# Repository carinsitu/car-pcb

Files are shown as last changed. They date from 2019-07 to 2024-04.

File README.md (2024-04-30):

# CarInSitu PCB for RC car

This repository contains _KiCAD_ files related to RC car's PCB.

Its licensed under _GPLv3_.

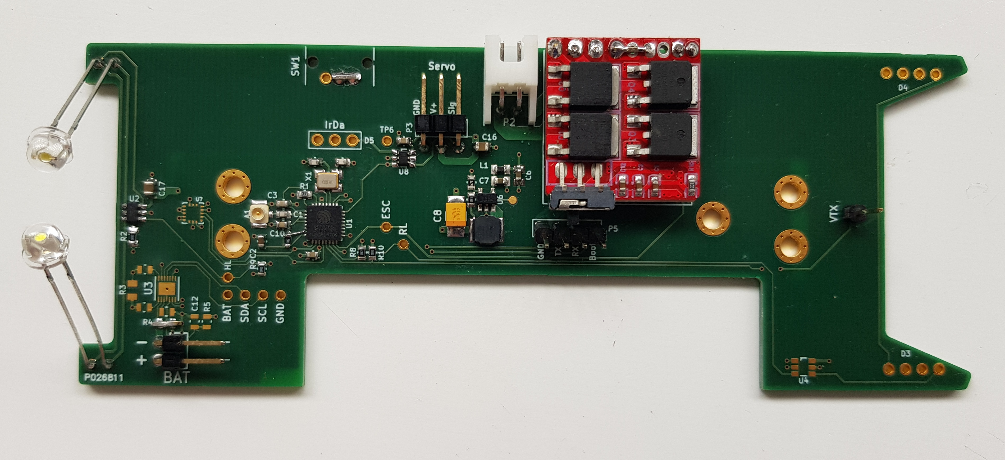
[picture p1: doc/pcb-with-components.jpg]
First Prototype


↑ The above photo is of proto 1

## Features

 - ESP82xx MCU
 - External antenna through UFL connector (using Lolin D1 mini pro)
 - Front head light (High-efficiency LEDs)
 - RBG LED port (APA106/WS2812)
 - PPM-driven ESC for brushed motor (external module based)
 - PPM-driven steering
 - IR receiver
 - VTX port (UART)
 - IMU
 - Battery gauge

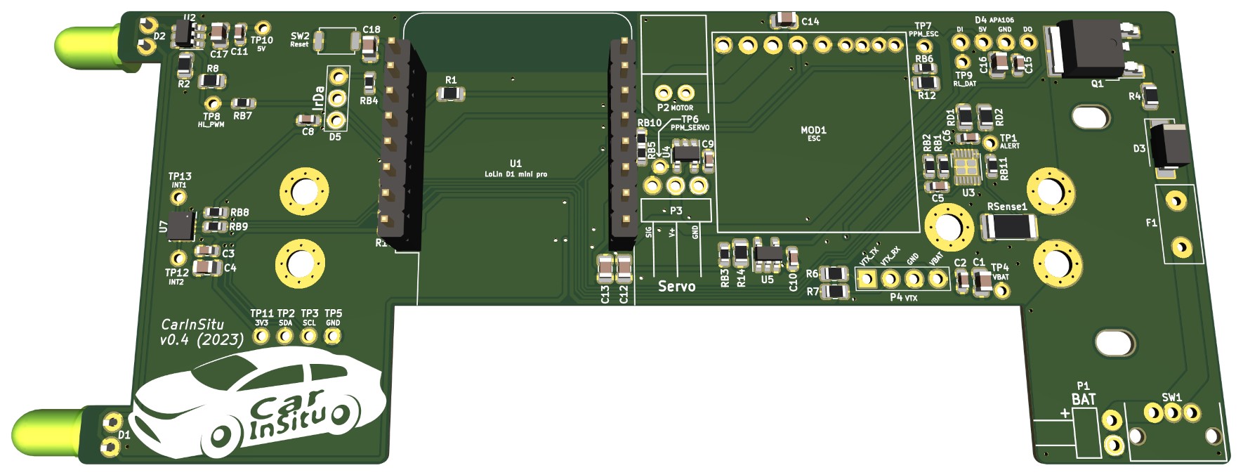
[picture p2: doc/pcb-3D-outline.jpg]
Preview of v0.4


↑ The above screenshot is a 3D preview of v0.4

## Manufacturing note

The PCB is designed with "standard" isolation (≥ 6 mil) for the most part, except in the area of the IMU (U7) whose package is just under 6 mil.

There are overlapping components:
- R1, C12, C13 with U1: U1 is high enough for this to work
- RB5 with RB10: one pad is common so that they are not on board together

## Misc

Note: Feel free to contact [neomilium](https://github.com/neomilium) if you want to turn this into commercial product.

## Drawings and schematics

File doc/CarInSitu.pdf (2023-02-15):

# SWITCH_SLIDE PWR_FLAG

LOLIN_RX_SWAP | Motor Control (ESC)

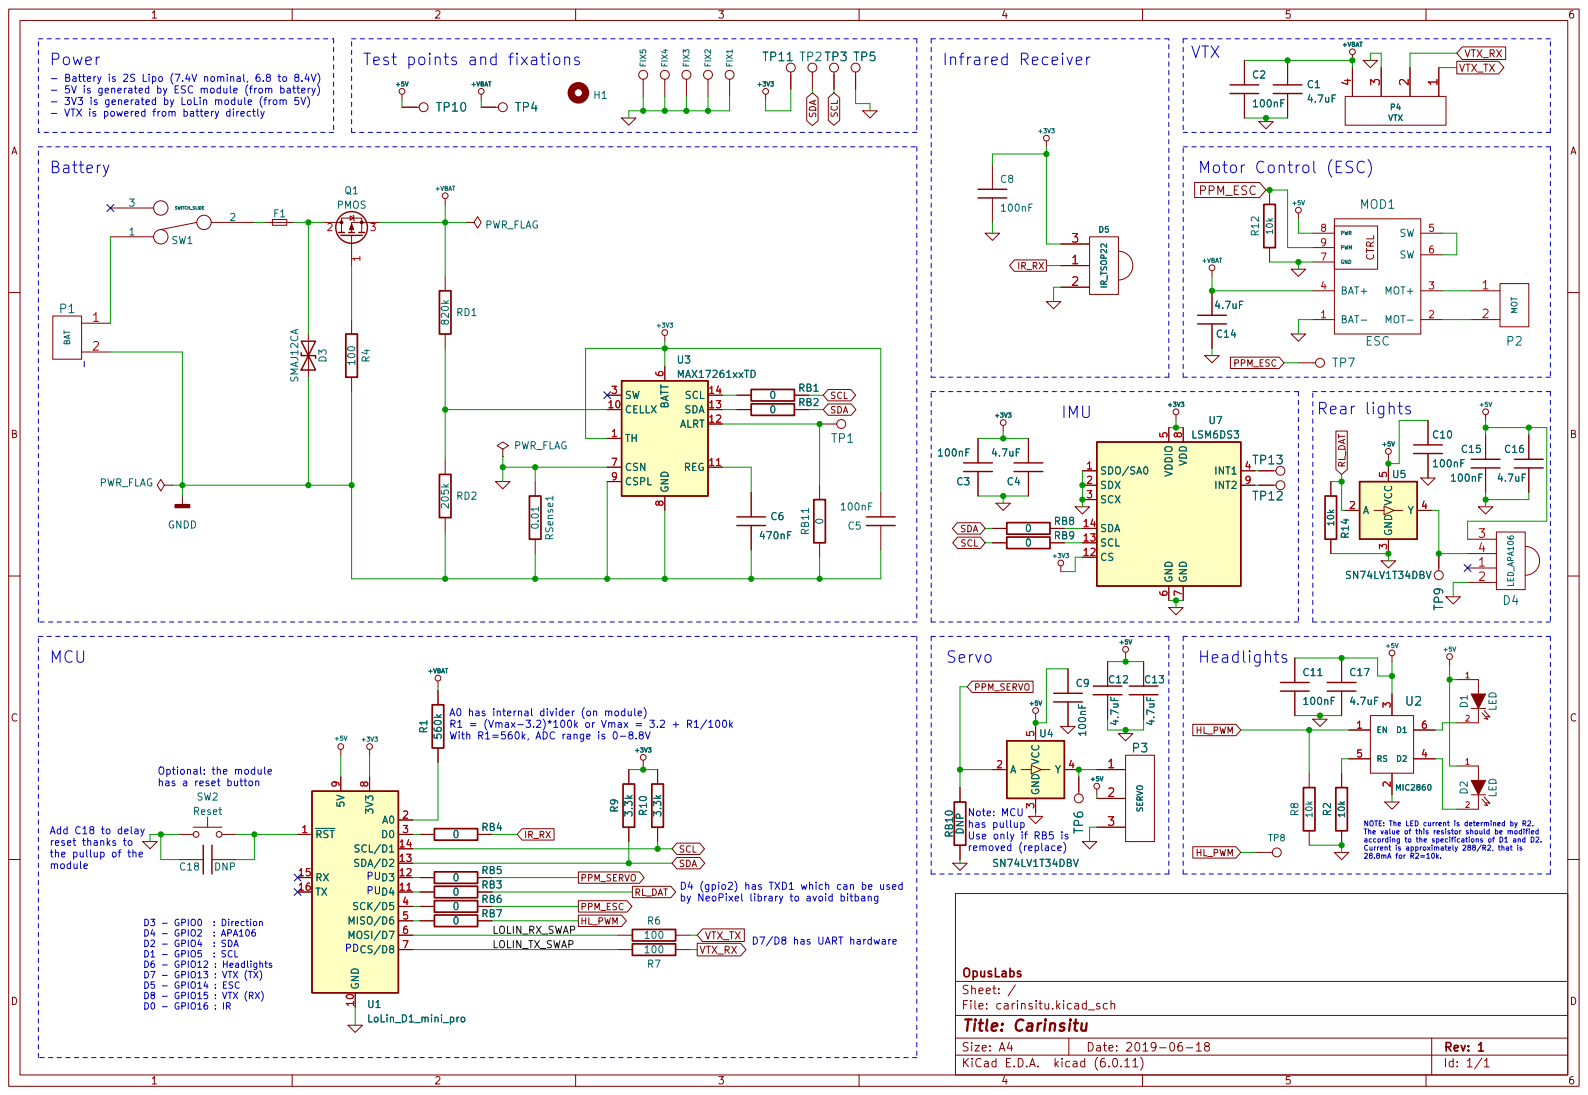
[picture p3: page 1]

Power
- VTX is powered from battery directly
the pullup of the module Battery

LSM6DS3 SDO/SA0 1 CS 12 SCL 13 SDA 14 SDX 2 SCX 3

3 SCK/D5 4 MISO/D6 5 MOSI/D7 6 CS/D8 7 ³V³

3 RB¹⁰ DNP
has pullup Use only if RB5 is

File: carinsitu.kicad_sch Sheet: / OpusLabs

References | Value | Distrib Ref Distributor | Manuf Ref | Manufacturer | Quantity
C2, C3, C5, C8, C9, C10, C11, C15 | 100nF | 2581045 | Farnell | C0603C104M4RACTU | Kemet | 8
C1, C4, C12, C13, C14, C16, C17 | 4.7uF | 2533952 | Farnell | 885012107013 | Würth elektronik | 7
C6 | 470nF | 2812270 | Farnell | 885012106015 | Würth elektronik | 1
C18 | DNP | - | - | - | - | 1
R2, R8, R12, R14 | 10k | 2073612 | Farnell | MCMR08X103JTL | Multicomp pro | 4
R4, R6, R7 | 100 | 2447552 | Farnell | MCWR08X1000FTL | Multicomp pro | 3
R9, R10 | 3.3k | 2073746 | Farnell | MCMR08X332JTL | Multicomp pro | 2
R1 | 560k | 2447685 | Farnell | MCWR08X5603FTL | Multicomp pro | 1
RD1 | 820k | 2447725 | Farnell | MCWR08X8203FTL | Multicomp pro | 1
RD2 | 205k | 2074399 | Farnell | MCSR08X2053FTL | Multicomp pro | 1
RSense1 | 0.01 | 2695180 | Farnell | MCWW20W0R01FTL | Multicomp pro | 1
RB10 | DNP | - | - | - | - | 1
D1, D2 | LED | 1716702 | Farnell | OVL-5521 | Multicomp pro | 2
D3 | SMAJ12CA | 2675283 | Farnell | SMAJ12CA+ | Multicomp pro | 1
D4 | LED_APA106 | | | | | 1
D5 | IR_TSOP22 | 4913073 | Farnell | TSOP2238 | Vishay | 1
U4, U5 | SN74LV1T34DBV | 218-4596 | RS | SN74LV1T34DBVR | Texas instruments | 2
U1 | LoLin_D1_mini_pro | | | Lolin D1 mini pro | Lolin | 1
U2 | MIC2860 | 2509995 | Farnell | MIC2860-2PYD6 | Microchip | 1
U3 | MAX17261xxTD | 2899544 | Farnell | MAX17261METD+ | Analog devices | 1
U7 | LSM6DS3 | 2664522 | Farnell | LSM6DSMTR | ST | 1
F1 | Fuse | 1345950 | Farnell | RGEF600 | LittelFuse | 1
SW1 | SWITCH_SLIDE | 2931770 | Farnell | L102011ML04Q | C&K Components | 1
SW2 | Reset | 3261823 | Farnell | SKRKAHE020 | Alps Alpine | 1
RB1, RB2, RB3, RB4, RB5, RB6, RB7, RB8, RB9, RB11 | 0 | 2447743 | Farnell | MCWR06X000PTL | Multicomp pro | 10
MOD1 | ESC | | | | | 1
Q1 | PMOS | 3518391 | Farnell | DMPH6050SK3-13 | Diodes inc. | 1
P1 | BAT | 2356176 | Farnell | 61300211021 | Würth elektronik | 1
P2 | MOT | 1516289 | Farnell | S2B-XH-A | JST | 1
P3 | SERVO | 3049557 | Farnell | 22-28-8030 | Molex | 1
P4 | VTX | - | - | - | - | 1

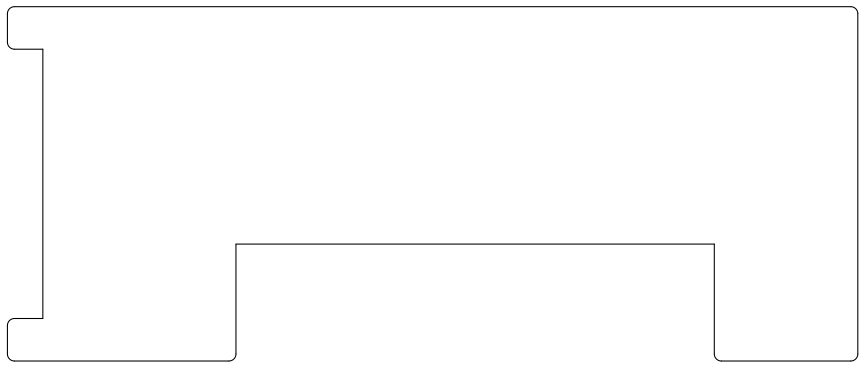
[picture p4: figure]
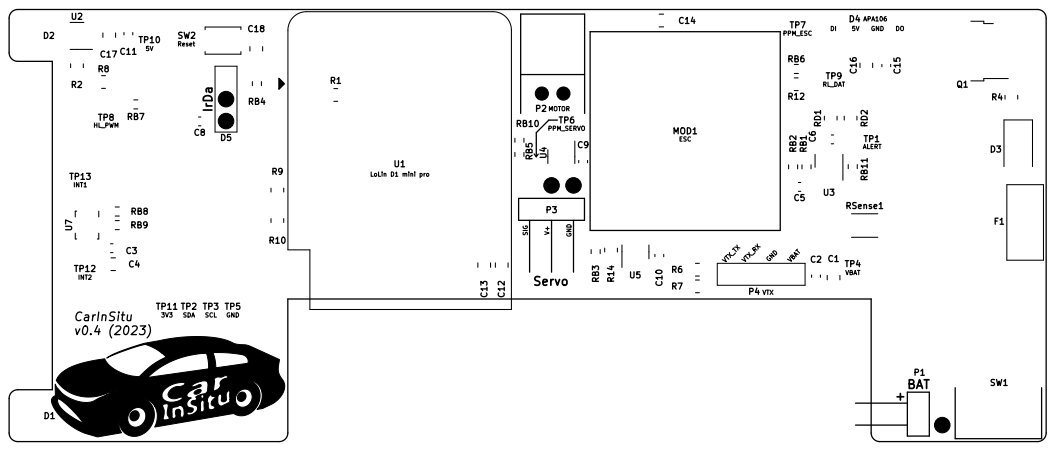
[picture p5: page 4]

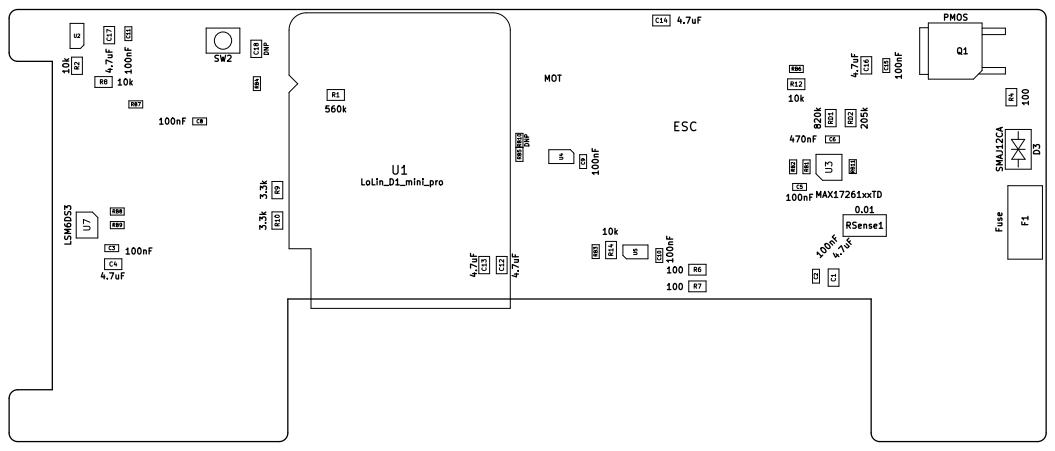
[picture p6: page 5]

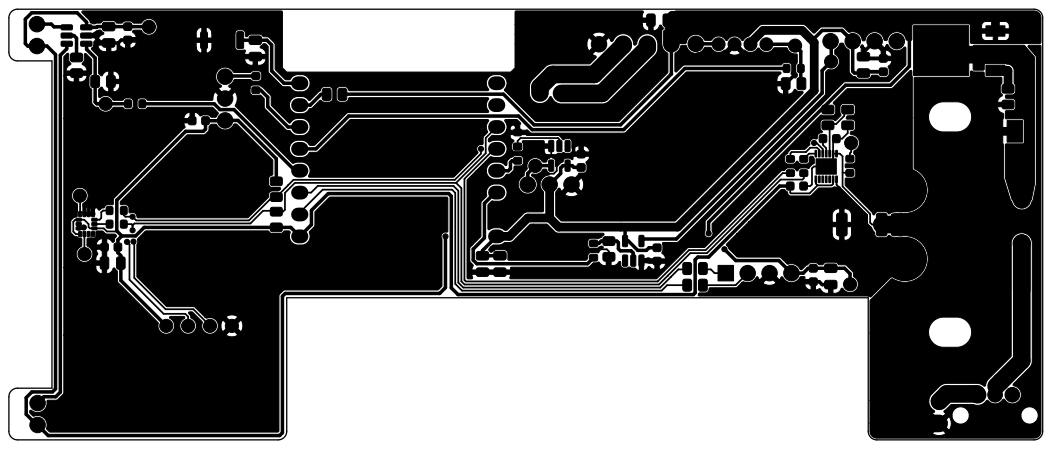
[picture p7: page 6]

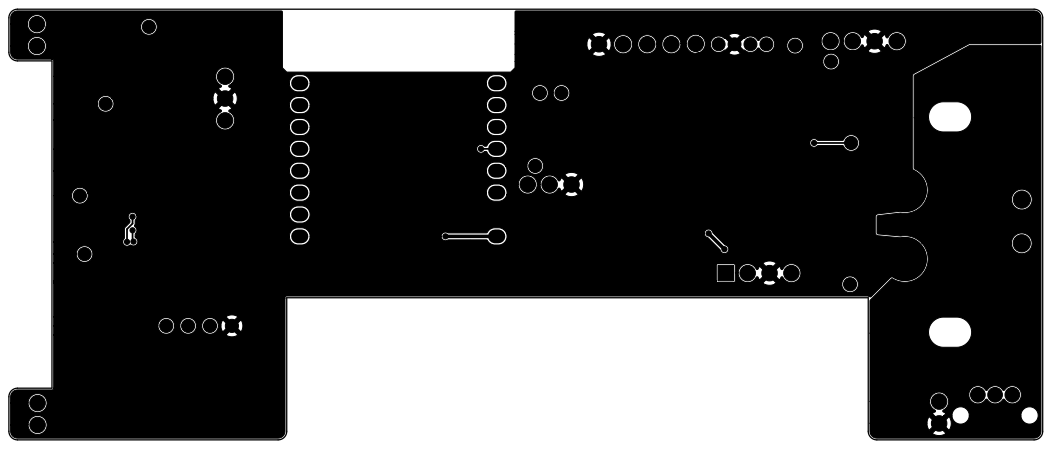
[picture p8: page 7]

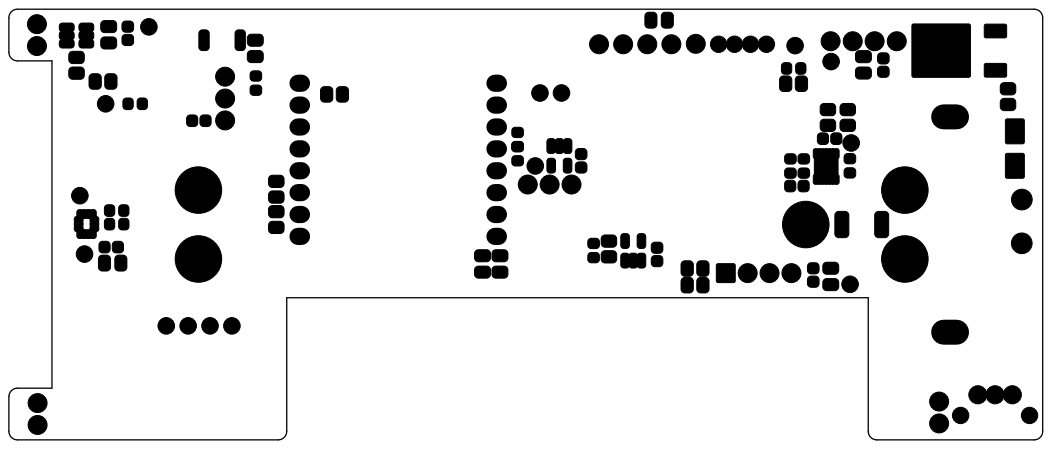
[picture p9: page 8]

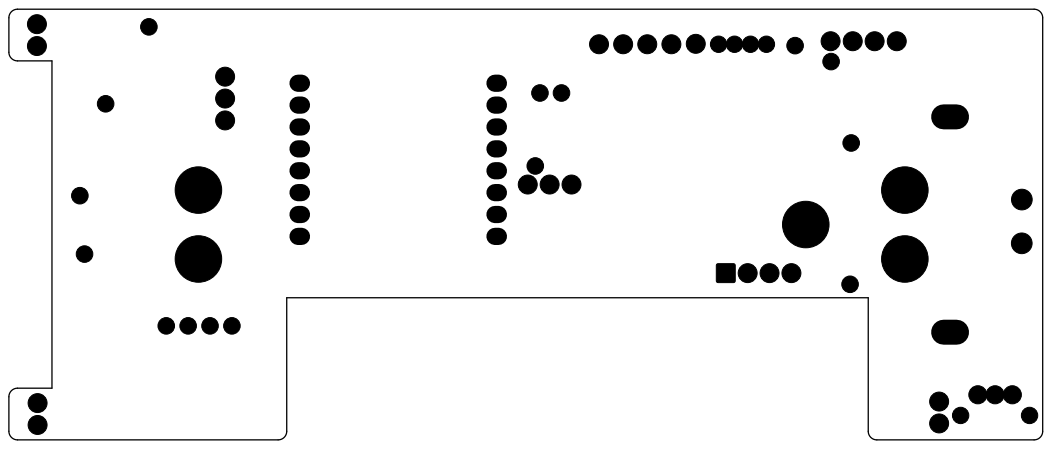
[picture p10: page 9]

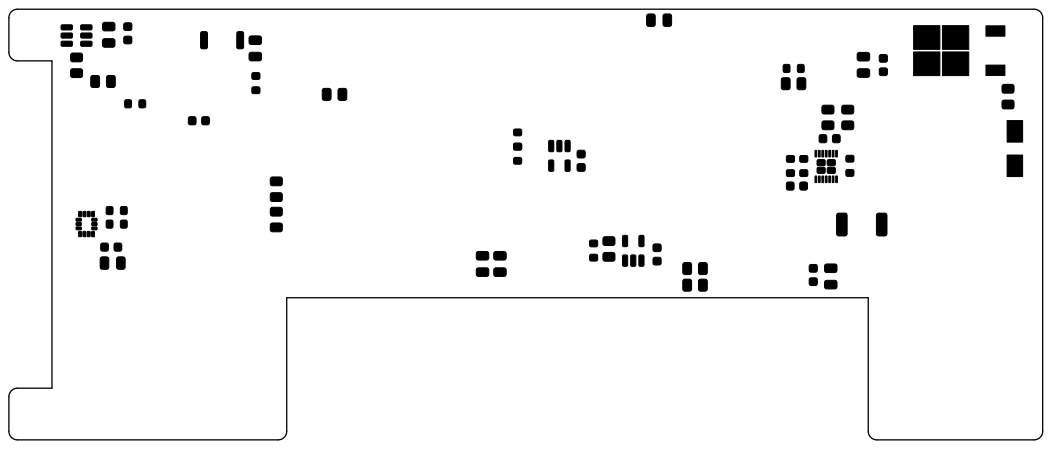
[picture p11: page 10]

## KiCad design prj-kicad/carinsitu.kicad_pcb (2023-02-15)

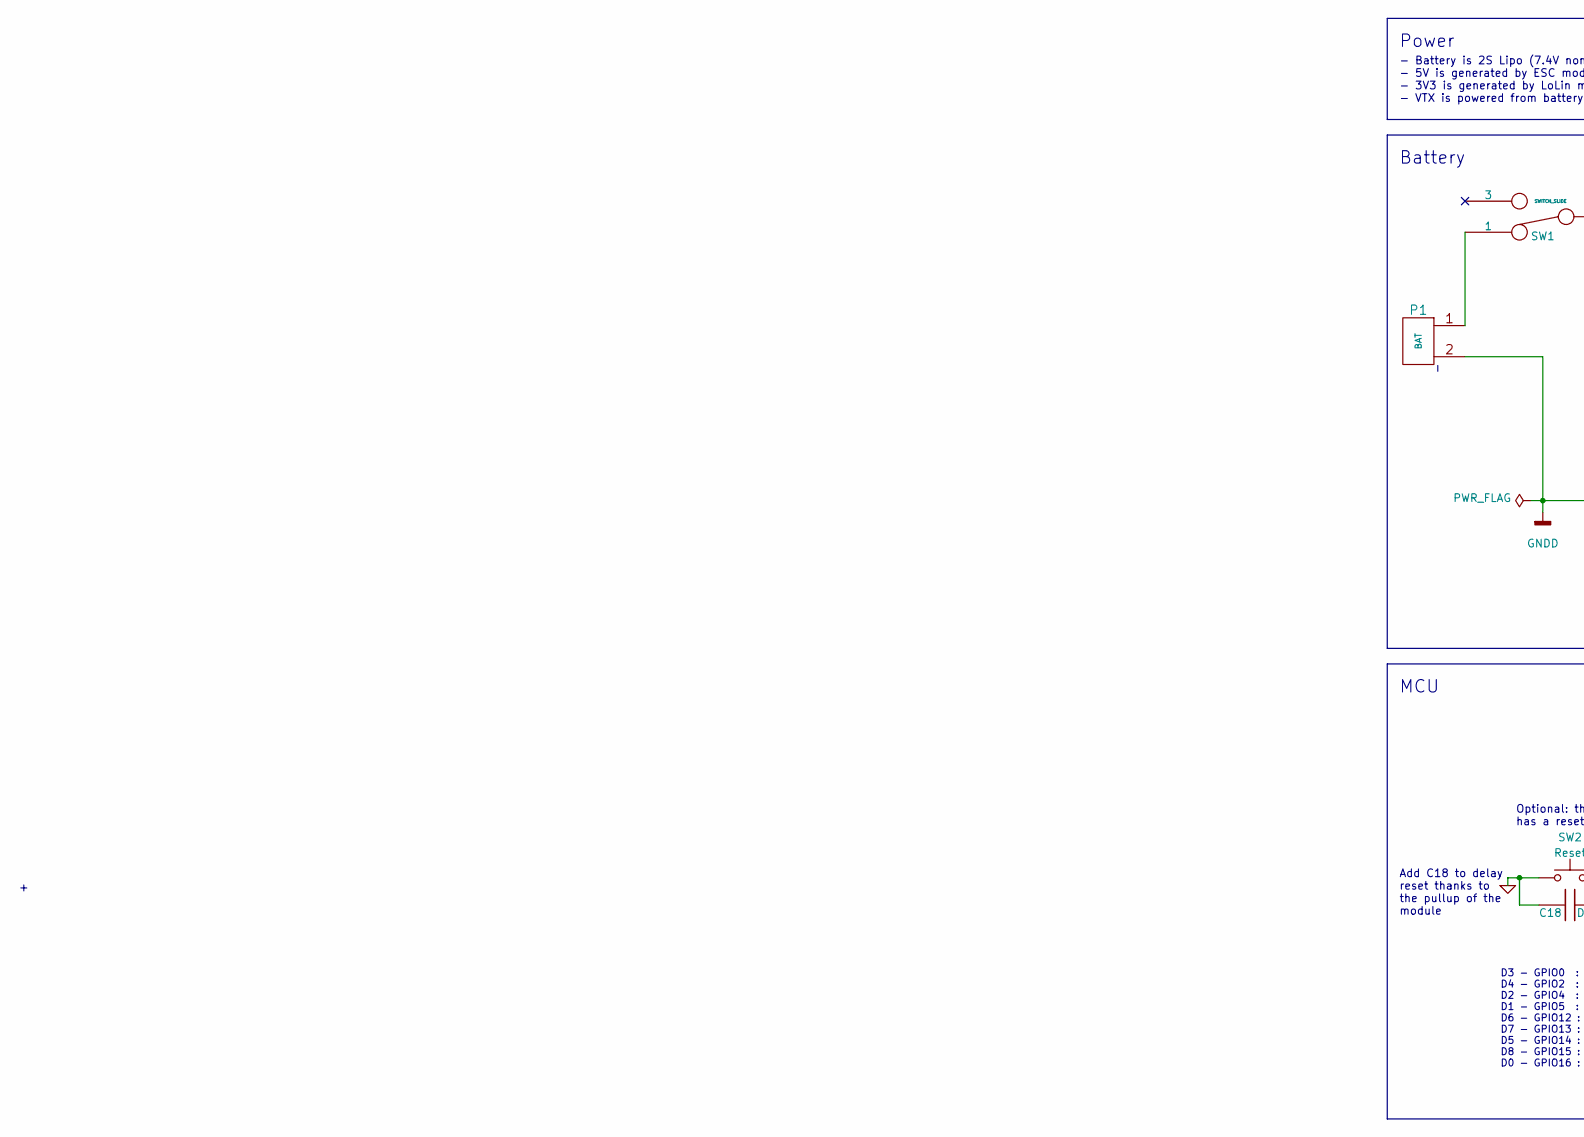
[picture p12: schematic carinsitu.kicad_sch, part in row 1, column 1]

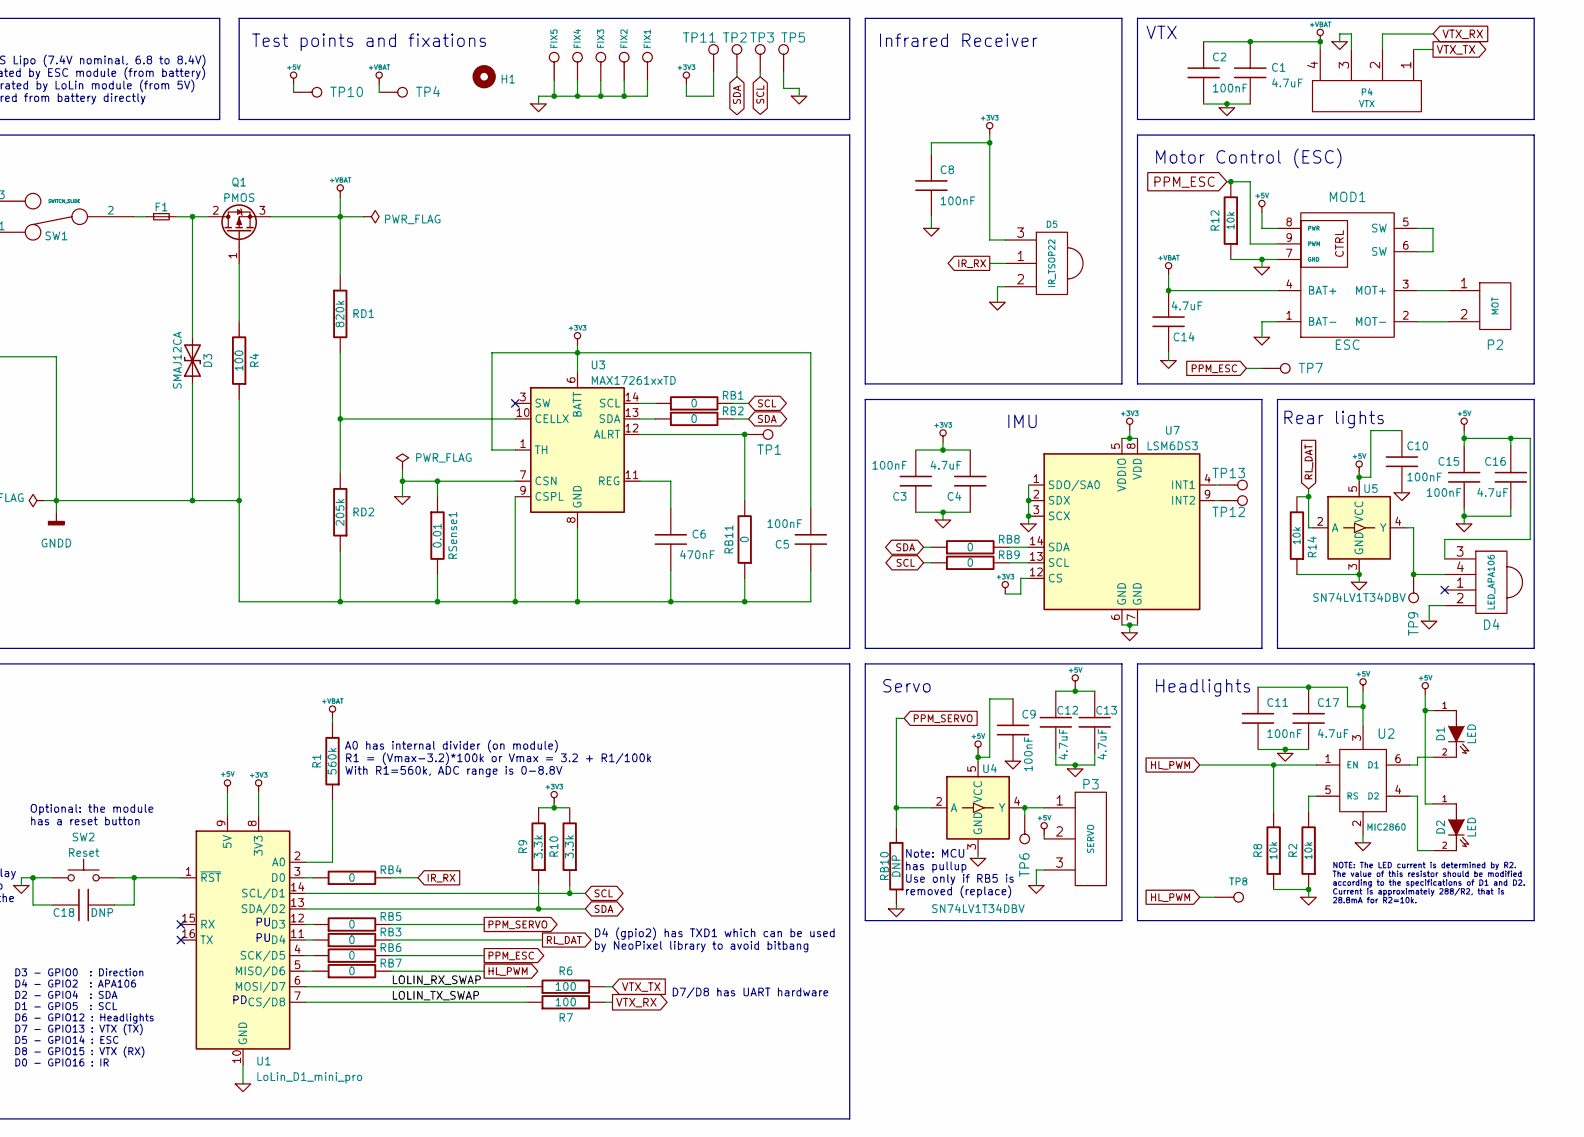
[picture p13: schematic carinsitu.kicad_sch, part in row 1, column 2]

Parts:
C1, C4, C12, C13, C14, C16, C17: 4.7uF; C_0805_2012Metric
C2, C3, C5, C8, C9, C10, C11, C15: 100nF; C_0603_1608Metric
C6: 470nF; C_0603_1608Metric
C18: DNP; C_0805_2012Metric
D1, D2: LED; LED_D5.0mm_Horizontal_O3.81mm_Z3.0mm
D3: SMAJ12CA; D_SMA
D4: LED_APA106; LED-APA106
D5: IR_TSOP22; CONN_61300311121
F1: Fuse; Fuse_Littelfuse_395Series
FIX1, FIX2, FIX3, FIX4, FIX5: CONN_1; FIX
H1: MountingHole; VTX_avatar_halfholes
MOD1: ESC
P1: BAT; CONN_61300211021
P2: MOT; CONN_JST-XH-2
P3: SERVO; CONN_61300311021
P4: VTX; CONN_61300411121
Q1: PMOS; TO-252-2
R1: 560k; R_0805_2012Metric
R2, R8, R12, R14: 10k; R_0805_2012Metric
R4, R6, R7: 100; R_0805_2012Metric
R9, R10: 3.3k; R_0805_2012Metric
RB1, RB2, RB3, RB4, RB5, RB6, RB7, RB8, RB9, RB11: 0; R_0603_1608Metric
RB10: DNP; R_0603_1608Metric
RD1: 820k; R_0805_2012Metric
RD2: 205k; R_0805_2012Metric
RSense1: 0.01; R_2010_5025Metric
SW1: SWITCH_SLIDE; SW_L102xxxML
SW2: Reset; SW_Push_SPST_NO_Alps_SKRK
TP1, TP2, TP3, TP4, TP5, TP6, TP7, TP8, TP9, TP10, TP11, TP12, TP13: CONN_1; TP
U1: LoLin_D1_mini_pro; WEMOS_D1_mini_light
U2: MIC2860; SOT-23-6
U3: MAX17261xxTD; TDFN-14-1EP_3x3mm_P0.4mm_EP1.78x2.35mm
U4, U5: SN74LV1T34DBV; SOT-23-5
U7: LSM6DS3; LGA-14_3x2.5mm_P0.5mm_LayoutBorder3x4y

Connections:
+3V3: C3.2, C4.2, C5.2, C8.1, D5.3 (VDD), R9.2, R10.2, TP11.1, U1.8 (3V3), U3.1 (TH), U3.6 (BATT), U7.5 (VDDIO), U7.8 (VDD), U7.12 (CS)
+5V: C9.1, C10.1, C11.1, C12.1, C13.1, C15.1, C16.1, C17.1, D1.1 (A), D2.1 (A), D4.3 (VDD), MOD1.8 (PWR), P3.2, TP10.1, U1.9 (5V), U2.3, U4.5 (VCC), U5.5 (VCC)
+VBAT: C1.1, C2.1, C14.2, MOD1.4 (BAT+), P4.4, Q1.3 (S), R1.2, RD1.1, TP4.1
/LOLIN_RX_SWAP: R6.1, U1.6 (MOSI/D7)
/LOLIN_TX_SWAP: R7.1, U1.7 (CS/D8)
GND: C1.2, C2.2, C3.1, C4.1, C8.2, C9.2, C10.2, C11.2, C12.2, C13.2, C14.1, C15.2, C16.2, C17.2, C18.1, D4.2 (GND), D5.2 (GND), FIX1.1, FIX2.1, FIX3.1, FIX4.1, FIX5.1, MOD1.1 (BAT-), MOD1.7 (GND), P3.3, P4.3, R2.1, R8.1, R12.1, R14.1, RB10.1, RSense1.1, SW2.1, TP5.1, U1.10 (GND), U2.2, U3.7 (CSN), U4.3 (GND), U5.3 (GND), U7.1 (SDO/SA0), U7.2 (SDX), U7.3 (SCX), U7.6 (GND), U7.7 (GND)
GNDD: C5.1, C6.2, D3.1 (A1), P1.2 (PM), R4.1, RB11.1, RD2.1, RSense1.2, U3.8 (GND), U3.9 (CSPL), U3.15 (GND)
HL_PWM: R8.2, RB7.2, TP8.1, U2.1 (EN)
IR_RX: D5.1 (DOUT), RB4.2
unnamed: C6.1, U3.11 (REG)
unnamed: C18.2, SW2.2, U1.1 (~RST)
unnamed: D1.2 (K), U2.6 (D1)
unnamed: D2.2 (K), U2.4 (D2)
unnamed: D3.2 (A2), F1.2, Q1.2 (D)
unnamed: D4.4 (DIN), TP9.1, U5.4 (Y)
unnamed: F1.1, SW1.2
unnamed: MOD1.2 (MOT-), P2.2 (PM)
unnamed: MOD1.3 (MOT+), P2.1
unnamed: MOD1.5 (SW), MOD1.6 (SW)
unnamed: P1.1, SW1.1
unnamed: P3.1, TP6.1, U4.4 (Y)
unnamed: Q1.1 (G), R4.2
unnamed: R1.1, U1.2 (A0)
unnamed: R2.2, U2.5 (RS)
unnamed: RB1.1, U3.14 (SCL)
unnamed: RB2.1, U3.13 (SDA)
unnamed: RB3.1, U1.11 (D4)
unnamed: RB4.1, U1.3 (D0)
unnamed: RB5.1, U1.12 (D3)
unnamed: RB6.1, U1.4 (SCK/D5)
unnamed: RB7.1, U1.5 (MISO/D6)
unnamed: RB8.2, U7.14 (SDA)
unnamed: RB9.2, U7.13 (SCL)
unnamed: RB11.2, TP1.1, U3.12 (ALRT)
unnamed: RD1.2, RD2.2, U3.10 (CELLX)
unnamed: TP12.1, U7.9 (INT2)
unnamed: TP13.1, U7.4 (INT1)
PPM_ESC: MOD1.9 (PWM), R12.2, RB6.2, TP7.1
PPM_SERVO: RB5.2, RB10.2, U4.2 (A)
RL_DAT: R14.2, RB3.2, U5.2 (A)
SCL: R10.1, RB1.2, RB9.1, TP3.1, U1.14 (SCL/D1)
SDA: R9.1, RB2.2, RB8.1, TP2.1, U1.13 (SDA/D2)
VTX_RX: P4.2, R7.2
VTX_TX: P4.1, R6.2

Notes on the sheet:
Optional: the module has a reset button
D7/D8 has UART hardware
MCU
A0 has internal divider (on module) R1 = (Vmax-3.2)*100k or Vmax = 3.2 + R1/100k With R1=560k, ADC range is 0-8.8V
Test points and fixations
NOTE: The LED current is determined by R2. The value of this resistor should be modified according to the specifications of D1 and D2. Current is approximately 288/R2, that is 28.8mA for R2=10k.
Motor Control (ESC)
D3 - GPIO0 : Direction D4 - GPIO2 : APA106 D2 - GPIO4 : SDA D1 - GPIO5 : SCL D6 - GPIO12 : Headlights D7 - GPIO13 : VTX (TX) D5 - GPIO14 : ESC D8 - GPIO15 : VTX (RX) D0 - GPIO16 : IR
Battery
Note: MCU has pullup Use only if RB5 is removed (replace)
Add C18 to delay reset thanks to the pullup of the module
Rear lights
VTX
D4 (gpio2) has TXD1 which can be used by NeoPixel library to avoid bitbang
Infrared Receiver
IMU
Headlights
Power
- Battery is 2S Lipo (7.4V nominal, 6.8 to 8.4V) - 5V is generated by ESC module (from battery) - 3V3 is generated by LoLin module (from 5V) - VTX is powered from battery directly
Servo

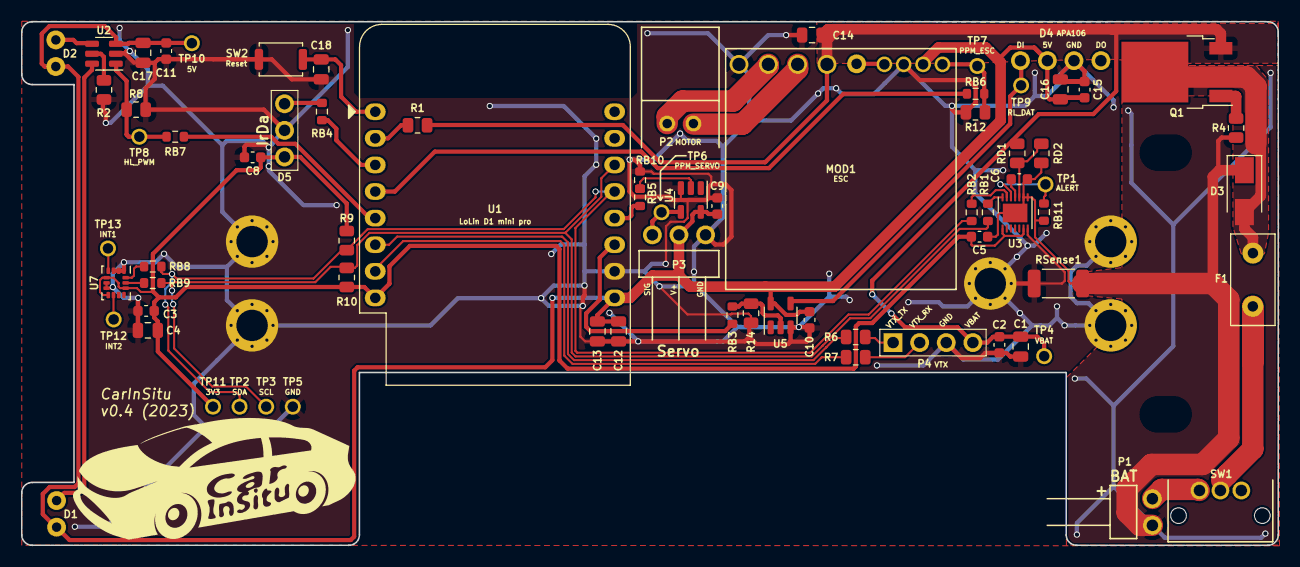
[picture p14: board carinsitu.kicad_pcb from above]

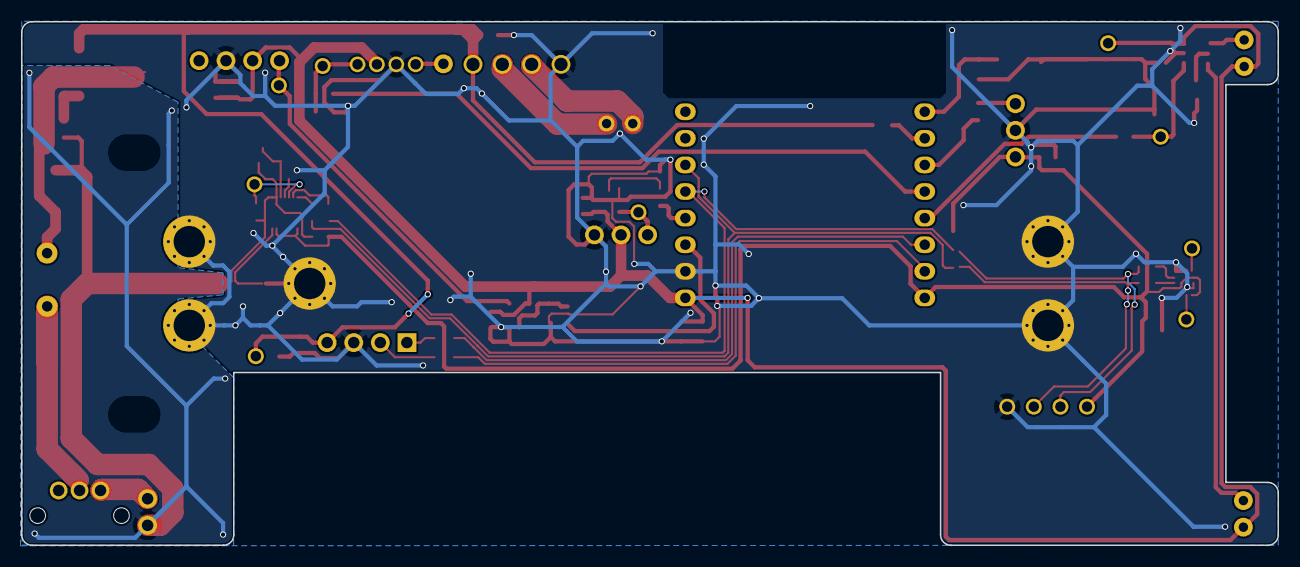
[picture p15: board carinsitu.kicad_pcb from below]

Board: 2 copper layers, 120.0 x 50.0 mm, 80 parts (2 on the bottom side), 44 nets.

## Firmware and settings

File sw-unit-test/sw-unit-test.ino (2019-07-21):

#include <ESP8266WiFi.h>
#include <ESP8266WebServer.h>
#include <ESP8266WiFiMulti.h>
#include <WiFiClient.h>
#include <Ticker.h>
#include <FS.h>

const char *base_ssid = "Carinsitu-01";
const char *base_password = "carinsitu0";

ESP8266WiFiMulti WiFiMulti;
ESP8266WebServer webServer(80);
IPAddress IP;
Ticker ts;

unsigned int s_value;
unsigned int led_value;

void handleRoot() {
  webServer.send(200, "text/html", "<h1>Hello Carinsitu World</h1>");
}

void printInfo() {
  Serial.print("AP IP address: ");
  Serial.println(IP);
  Serial.printf("Connection status: %d\r\n", WiFi.status());
  WiFi.printDiag(Serial);

  if (led_value)
  {
    digitalWrite(0, LOW);
    led_value = 0;
  }
  else
  {
    digitalWrite(0, HIGH);
    led_value = 1;
  }
}

void setup() {
  pinMode(0, OUTPUT); // Headlight
  pinMode(5, OUTPUT); // Servo
  Serial.begin(115200);
  Serial.setDebugOutput(true);
  
  delay(1000);
  led_value = 0;
  s_value = 100;
  
  Serial.println();
  Serial.println("CarInSitu ESP8285 unit-test");

  IPAddress ip(192, 168, 49, 1);
  IPAddress gateway(192, 168, 49, 1);
  IPAddress subnet(255, 255, 255, 0);
  
  WiFi.mode(WIFI_AP);
  
  WiFi.softAPConfig(ip, gateway, subnet);
  WiFi.softAP(base_ssid, base_password);
  
  IP = WiFi.softAPIP();
  Serial.print("AP IP address: ");
  Serial.println(IP);
  
  webServer.on("/", handleRoot);

  webServer.begin();
  Serial.println("HTTP server started");

  digitalWrite(0, LOW);  // HL: Lights are off
  digitalWrite(5, HIGH); // Servo : set "1" to test level shifter

  ts.attach(3, printInfo);
}

void loop() {
  String rxStr;
  webServer.handleClient();
  if (Serial.available() > 0)
  {
    rxStr = Serial.readStringUntil('\n');
    s_value = rxStr.toInt();
  }
}

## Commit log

2019-06-18 --=={ Create Project }==--
    [carinsitu.kicad_pcb, carinsitu.sch]
2019-06-18 = ADD: Draw board outline, add fix holes
    [carinsitu.kicad_pcb, carinsitu.sch]
2019-06-26 = ADD: Place headlight LEDs, motor connector and ESC outline
    [carinsitu.kicad_pcb, carinsitu.sch]
2019-07-01 = ADD: Create ESP32 interface ; create schematics and footprint for Wemos D1-Mini (not fully routed)
    [carinsitu.kicad_pcb, carinsitu.sch]
2019-07-03 = ADD: Insert a slide switch to connect power (on / off)
    [carinsitu.kicad_pcb, carinsitu.sch]
2019-07-03 = ADD: Insert battery monitor (STC3100)
    [carinsitu.kicad_pcb, carinsitu.sch]
2019-07-03 = ADD: insert a 3 pin connector for servo (direction)
    [carinsitu.kicad_pcb, carinsitu.sch]
2019-07-03 = ADD: insert second RGB led and add a level switch (3V3 -> 5V) on data line
    [carinsitu.kicad_pcb, carinsitu.sch]
2019-07-03 = CLEAN: Re-order schematic blocks and add comments
    [carinsitu-power.sch, carinsitu.sch]
2019-07-03 = ADD: insert a 3V3 power regulator. Schematic and place ok, routing not complete
    [carinsitu-power.sch, carinsitu.kicad_pcb, carinsitu.sch]
2019-07-03 = ADD: insert iNEMO inertial chip (LSM6DS3) - Routing not complete
    [carinsitu-power.sch, carinsitu.kicad_pcb, carinsitu.sch]
2019-07-05 = UPD: Improve RGB LED position (according to CAD specs) and power routing
    [carinsitu.kicad_pcb, carinsitu.sch]
2019-07-05 = UPD: Replace ESP32 with ESP82xx to fit software requirements
    [carinsitu-power.sch, carinsitu.kicad_pcb, carinsitu.sch]
2019-07-08 = UPD: Improve ESP82xx routing, connect main IOs (leds, esc, servo, ...)
    [carinsitu-power.sch, carinsitu.kicad_pcb, carinsitu.sch]
2019-07-09 = UPD: Move power button and servo connector
    [carinsitu.kicad_pcb]
2019-07-10 = UPD: Replace battery gauge (STC3100 limited to 1 cell) by a MAX17205 ic
    [carinsitu-power.sch, carinsitu.kicad_pcb, carinsitu.sch]
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2019-07-10 = ADD: Insert test points for I2C and battery (2.54 grid)
    [carinsitu-power.sch, carinsitu.kicad_pcb, carinsitu.sch]
2019-07-15 = UPD: Improve power (add decoupling caps), Add test-points for main signals, Add a level shifter for servo
    [carinsitu-power.sch, carinsitu.kicad_pcb, carinsitu.sch]
2019-07-16 = UPD: Improve power, fix 3V3 reg footprint and add routing
    [carinsitu-power.sch, carinsitu.kicad_pcb, carinsitu.sch]
2019-07-16 = UPD: Improve U3 routing (bat gauge) reduce soldermask and solderpaste for a better isolation
    [carinsitu.kicad_pcb]
2019-07-17 = ADD: Generate production files for PCB (Gerber + drill)
    [carinsitu-B.Cu.gbr, carinsitu-B.Mask.gbr, carinsitu-Edge.Cuts.gbr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]
2019-07-17 = UPD: Add extra-informations on schematics for BOM
    [carinsitu.sch]
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2019-08-09 = UPD: Rotate headlights LEDs
    [carinsitu.kicad_pcb]
2019-08-09 = UPD: Move headlights driver and add a logic ic to invert signal
    [carinsitu-power.sch, carinsitu.kicad_pcb, carinsitu.sch]
2023-01-05 Move a lot of components on the PCB to the right
    [carinsitu.kicad_pcb]
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2023-01-07 Update KiCAD project to recent version (6.0)
    [carinsitu-power.kicad_sch, carinsitu-power.sch, carinsitu.kicad_sch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]
2023-01-07 Fix schematic DRC
    [carinsitu-power.kicad_sch, carinsitu.kicad_sch]
2023-01-07 Sync PCB with schematic
    [carinsitu.kicad_pcb]
2023-01-07 Do TODO for rear lights
    [carinsitu.kicad_pcb, carinsitu.kicad_sch]
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2023-01-07 Move components listed in TODO
    [carinsitu.kicad_pcb]
2023-01-07 Do the remaining TODO list
    [carinsitu.kicad_pcb, carinsitu.kicad_sch]
2023-01-07 Add logo on PCB
    [carinsitu.kicad_pcb]
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2023-01-09 Reduce length of the board
    [carinsitu.kicad_pcb]
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2023-01-21 Change MCU and VTX + related (see detailed message)
    The VTX module is changed and now communicates with an UART.
    The MCU and its powering are replaced by a LoLin D1 mini pro module.
    IO are remapped
    Removed inverter on headlights (not needed with new mapping)
    Added pull-up on I²C and pull-down on ESC and Headlights
    [carinsitu-power.kicad_sch, carinsitu.kicad_sch]
2023-01-21 Add precisions in note for headlights
    [carinsitu.kicad_sch]
2023-01-21 Add spacer in PCB comment layer to have its shape displayed
    [carinsitu.kicad_pcb]
2023-01-24 Add zero ohm resistors
    [carinsitu.kicad_sch]
2023-01-24 Redesign IMU connections
    [carinsitu.kicad_sch]
2023-01-26 review MAX17205 Fuel Gauge Add missing cap values
    [carinsitu.kicad_sch]
2023-01-27 Update PCB + schematic adjustments
    Notable schematic changes:
    - change level shifters for SN74LV1T34DBV (simplify routing)
    - add fuse inversion protection
    [carinsitu.kicad_pcb, carinsitu.kicad_sch]
2023-01-30 Change battery monitor MAX17044G in schematic
    [carinsitu.kicad_sch]
2023-01-30 Route new battery monitor
    [carinsitu.kicad_pcb]
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2023-01-31 Move components that were under the ESC outside
    [carinsitu.kicad_pcb]
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2023-02-01 Move P3 (servo connector)
    [carinsitu.kicad_pcb]
2023-02-01 Move IrDa connector and reset button under the windscreen of the car
    [carinsitu.kicad_pcb]
2023-02-01 Move U5 and other mods
    [carinsitu.kicad_pcb]
2023-02-03 Change some footprints for kicad lib ones + silkscreen + route adjustments
    [carinsitu.kicad_pcb, carinsitu.kicad_sch]
2023-02-03 Add decoupling capacitors + RB10
    [carinsitu.kicad_pcb, carinsitu.kicad_sch]
2023-02-03 Move U3 and its companions
    [carinsitu.kicad_pcb]
2023-02-03 Add VTX holes (WIP, bottom right needs rerouting)
    [carinsitu.kicad_pcb, carinsitu.kicad_sch]
2023-02-05 Change input protection and its routing
    [carinsitu.kicad_pcb, carinsitu.kicad_sch]
2023-02-05 Adjust small things on PCB
    [carinsitu.kicad_pcb]
2023-02-06 Move VTX holes slightly + adjust around BAT connector
    [carinsitu.kicad_pcb]
2023-02-06 Move Servo connector out of spacer + invert Motor connector to gain place
    [carinsitu.kicad_pcb, carinsitu.kicad_sch]
2023-02-07 Add other decoupling capacitors and route them
    [carinsitu.kicad_pcb, carinsitu.kicad_sch]
2023-02-07 Fix GND pin type of ESC
    [carinsitu.kicad_sch]
2023-02-07 Add TVS diode protection
    [carinsitu.kicad_pcb, carinsitu.kicad_sch]
2023-02-07 Reroute 5V to clear U1 module antenna zone
    [carinsitu.kicad_pcb]
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2023-02-07 Add reset capacitor
    [carinsitu.kicad_pcb, carinsitu.kicad_sch]
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2023-02-09 schematic corrections and first PCB update
    [Power.kicad_sch, carinsitu.kicad_pcb, carinsitu.kicad_sch]
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2023-02-12 Change schematic to have everything on one page
    [Power.kicad_sch, carinsitu.kicad_sch]
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2023-02-12 Remove thermal pad around fixation holes
    [carinsitu.kicad_pcb]
2023-02-12 Populate most info for BOM, and update PCB
    [carinsitu.kicad_pcb, carinsitu.kicad_sch]
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2023-02-13 Fix net names and isolation rule for IMU on PCB
    [carinsitu.kicad_pcb]
2023-02-13 Fix Fab layer readability
    [carinsitu.kicad_pcb]
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2023-02-15 Fix a manufacturer's name in bom
    [carinsitu.kicad_sch]
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
